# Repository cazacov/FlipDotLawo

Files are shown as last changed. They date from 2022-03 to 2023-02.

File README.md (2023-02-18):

# FlipDot34

Controller for the flip-dot display with 34-pin connector. For example produced by Lawo-Luminator-Europa Mark IV Industries GmbH.

Version 28x19
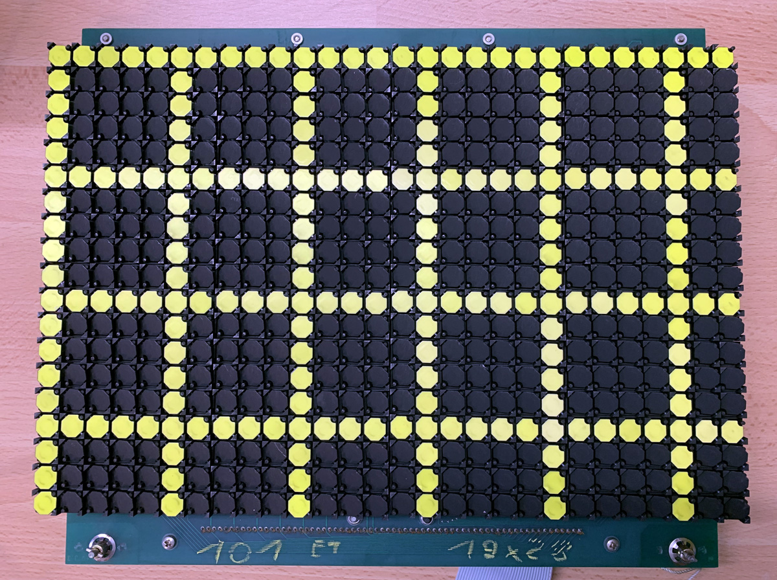
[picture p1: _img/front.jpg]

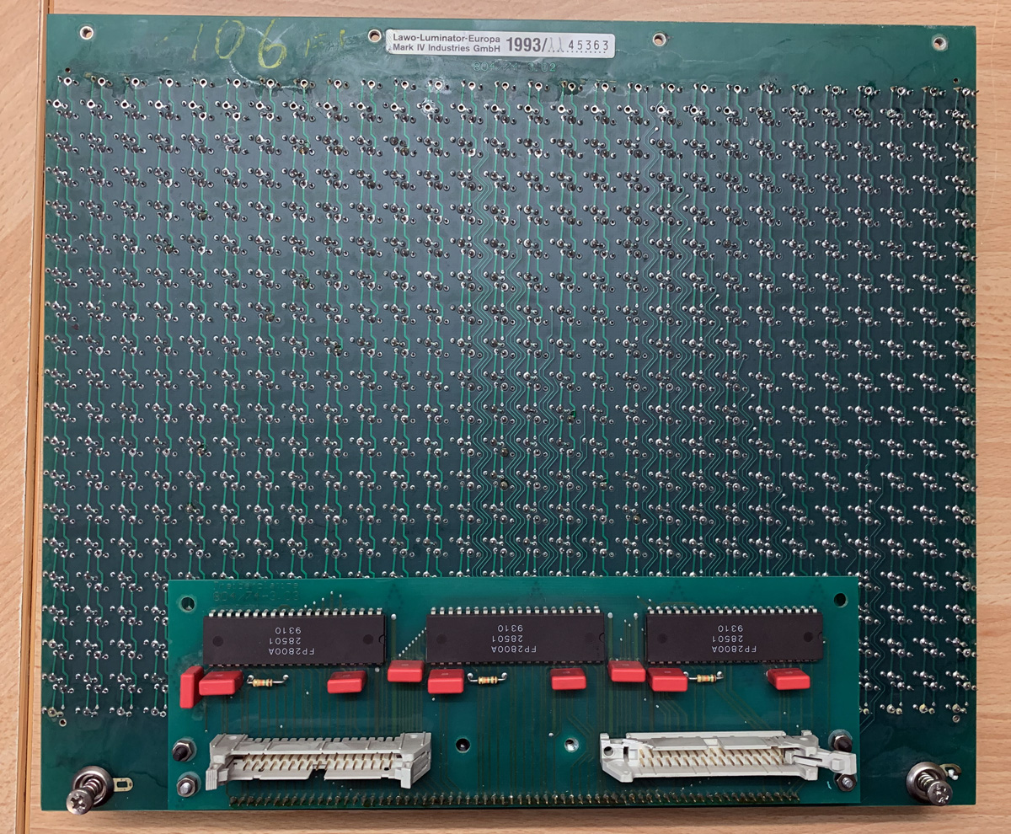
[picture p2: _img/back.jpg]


Version 28x24 with LED lights
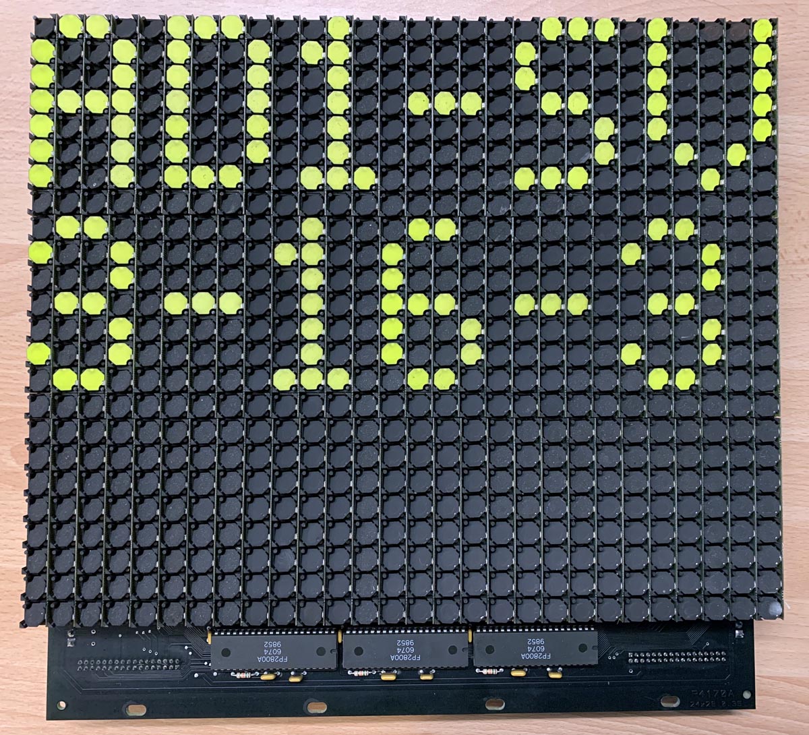
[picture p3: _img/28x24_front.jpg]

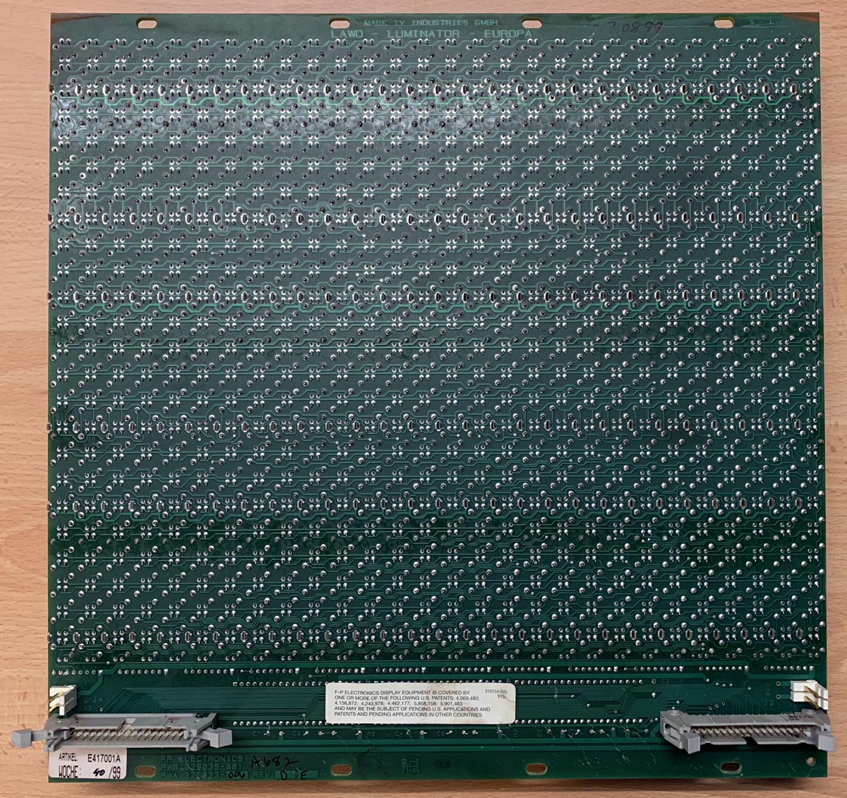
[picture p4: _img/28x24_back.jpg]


## Connector Pinout
| Pin |  Function | Pin |  Function |
| --- | --- | --- | --- |
| 1 | GND  | 2 | GND  | 
| 3 | GND  | 4 | GND  | 
| 5 | 5V  |  6 | 5V  | 
| 7 | A0-X | 8 | DATA-X |
| 9 | A1-X | 10 | ENABLE-Y-SET |
| 11 | A2-X | 12 | ENABLE-Y-RESET |e
| 13 | B0-X | 14 | ENABLE-X-1 |
| 15 | B1-X | 16 | ENABLE-X-2 |
| 17 | A0-Y | 18 | ENABLE-X-3 |
| 19 | A1-Y | 20 | ENABLE-X-4 |
| 21 | A2-Y | 22 | ENABLE-X-5 |
| 23 | B0-Y | 24 | ENABLE-X-6 |
| 25 | B1-Y | 26 | ENABLE-X-7 |
| 27 | n/c | 28 | ENABLE-X-8 |
| 29 | 24V  |  30 | 24V  | 
| 31 | GND  | 32 | GND  | 
| 33 | GND  | 34 | GND  | 

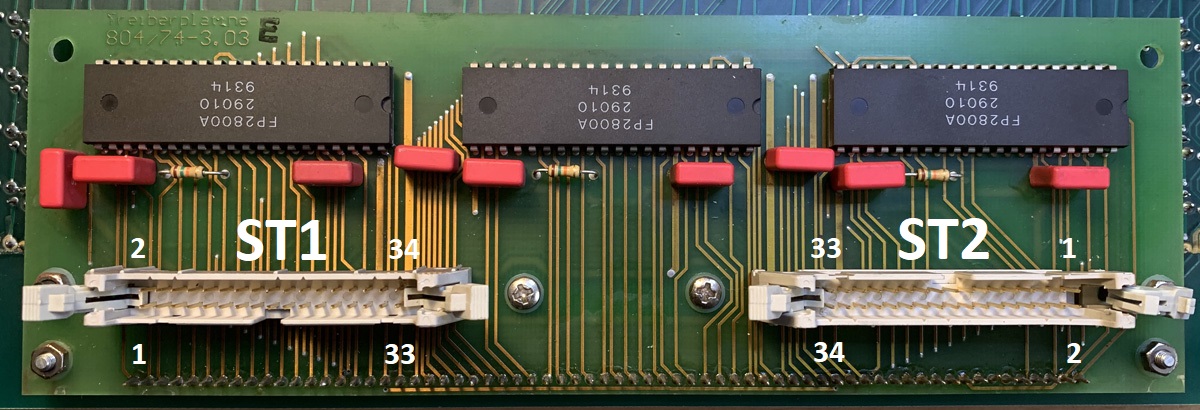
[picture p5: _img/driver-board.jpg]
Matrix driver


## Chaining Multiple Displays in a Row

Driver board has two connectors. The output connector ST2 mostly duplicates 1:1 singnals from the input ST1 but ENABLE-X- signals are shifted. 

| Pin | INPUT  ST1 |  OUTPUT ST2 |
| --- | --- | --- |
| 13  | ENABLE-X-1 | ENABLE-X-2 |
| 15  | ENABLE-X-2 | ENABLE-X-3 |
| 17  | ENABLE-X-3 | ENABLE-X-4 |
| 19  | ENABLE-X-4 | ENABLE-X-5 |
| 21  | ENABLE-X-5 | ENABLE-X-6 |
| 23  | ENABLE-X-6 | ENABLE-X-7 |
| 25  | ENABLE-X-7 | ENABLE-X-8 |
| 17  | ENABLE-X-8 | ENABLE-X-1 |

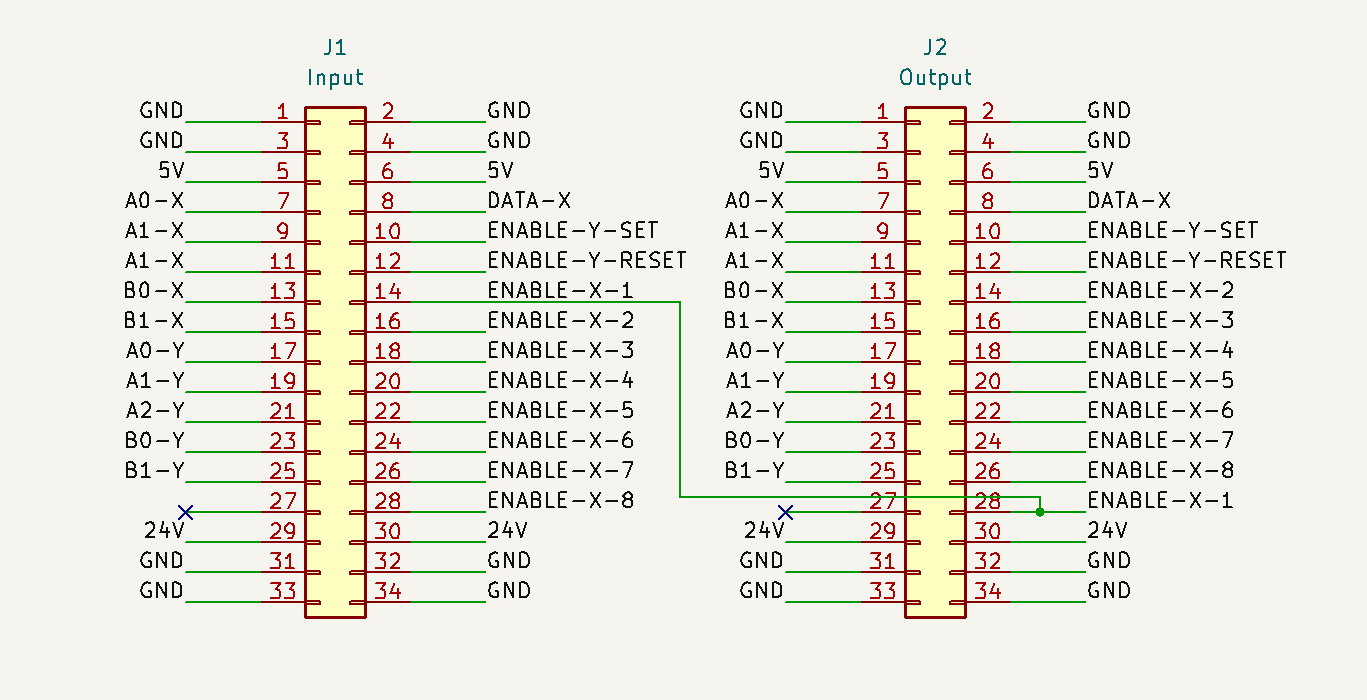
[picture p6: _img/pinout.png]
Pinout


The ENABLE input of FP2800 X Driver is always connected to ENABLE-X-1 connector pin. For example when ENABLE-X-3 is set to HIGH the first two displays in a row will ignore it, but after two decrements the signal will be applied to ENABLE-X-1 ST1 of the third display matrix and will activate it.

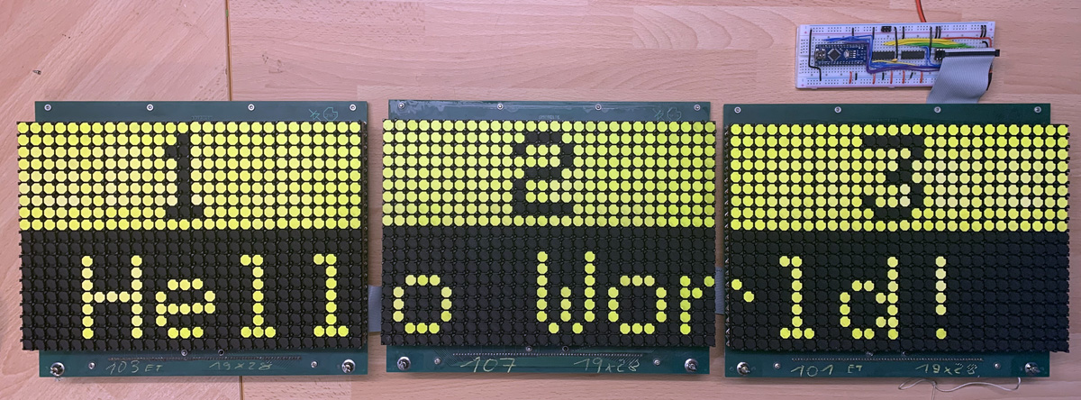
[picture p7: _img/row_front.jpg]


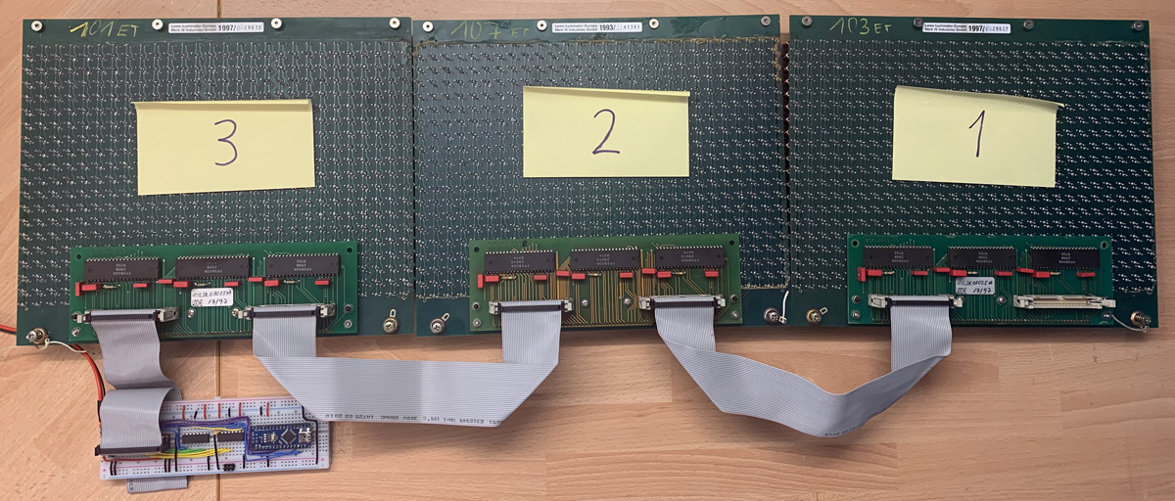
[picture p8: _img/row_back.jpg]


## Driver Boards

### Prototype

This prototype uses Arduino Nano and two 74HC595 shift registers to control up to 6 matrices. By adding another 595 it can control up to 8 display matrices.

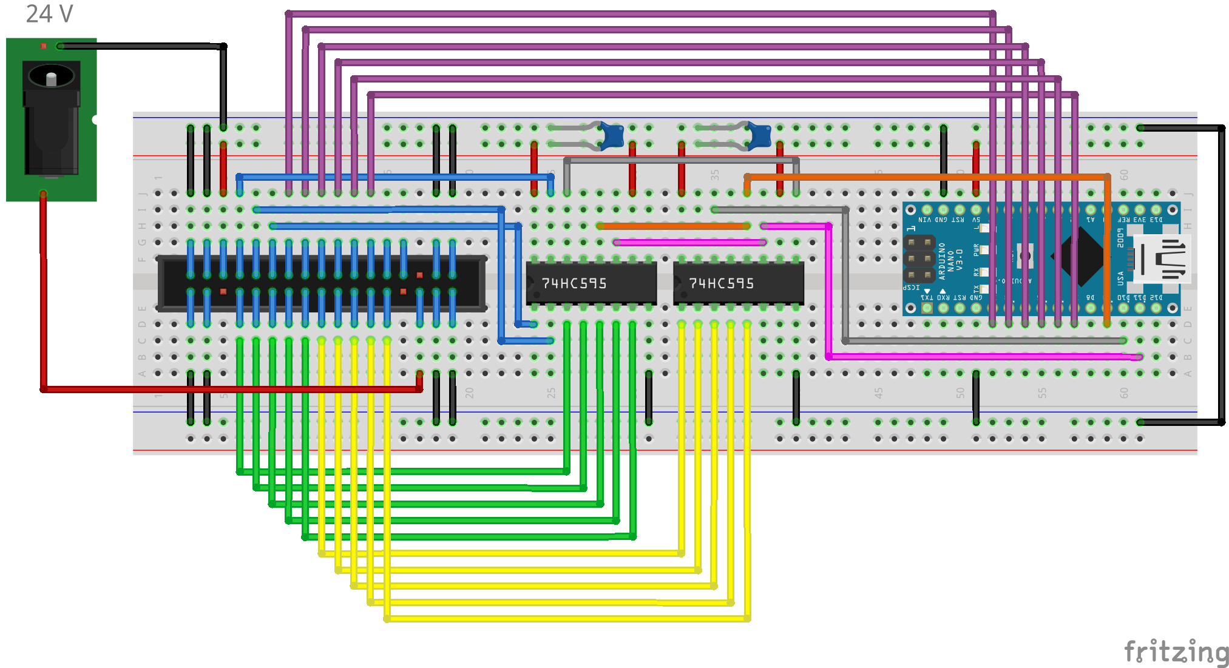
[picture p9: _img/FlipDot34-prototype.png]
Prototype


### FlipDot34Nano

Driver board with Arduino Nano and three 74HC595 shift registers opitmized for single-sided PCB that can be milled with 3018 CNC. 3 digital pins are used for controlling shift registers, analog pins A4 and A5 can be used to receive commands over I2C. Pins A0-A2 connected to DIP switches choosing I2C address.

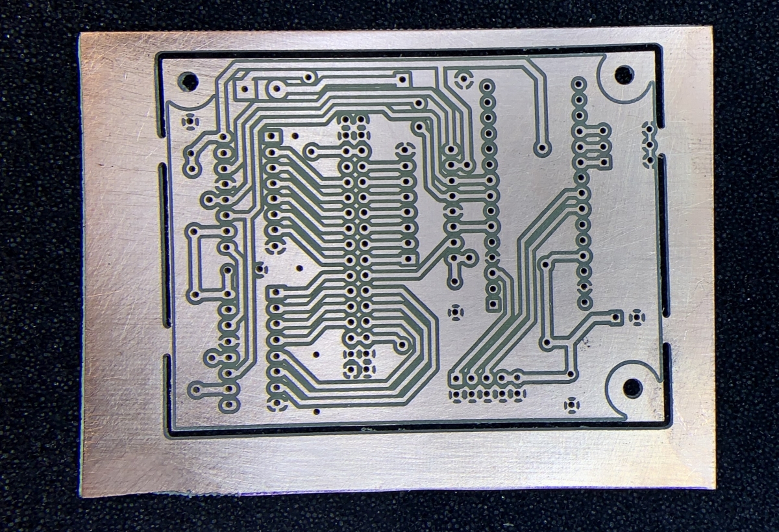
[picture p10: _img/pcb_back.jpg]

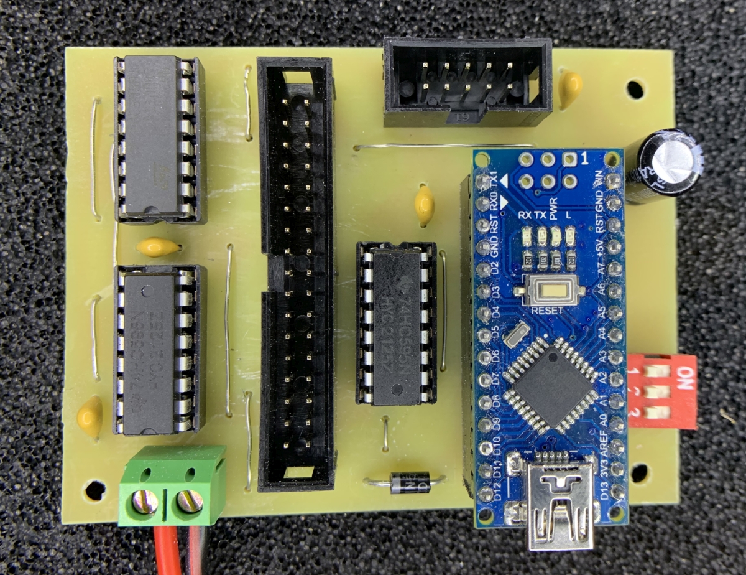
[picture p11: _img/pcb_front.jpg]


Schematic in KiCad 6 format checked in under .\Driver-boards\FlipDot34Nano\schematic\FlipDot34Nano

---
All trademarks, logos and brand names are the property of their respective owners. All company, product and service names are for identification purposes only. 

It's a hobby project; I am not affiliated with any  company producing flip-dot displays.

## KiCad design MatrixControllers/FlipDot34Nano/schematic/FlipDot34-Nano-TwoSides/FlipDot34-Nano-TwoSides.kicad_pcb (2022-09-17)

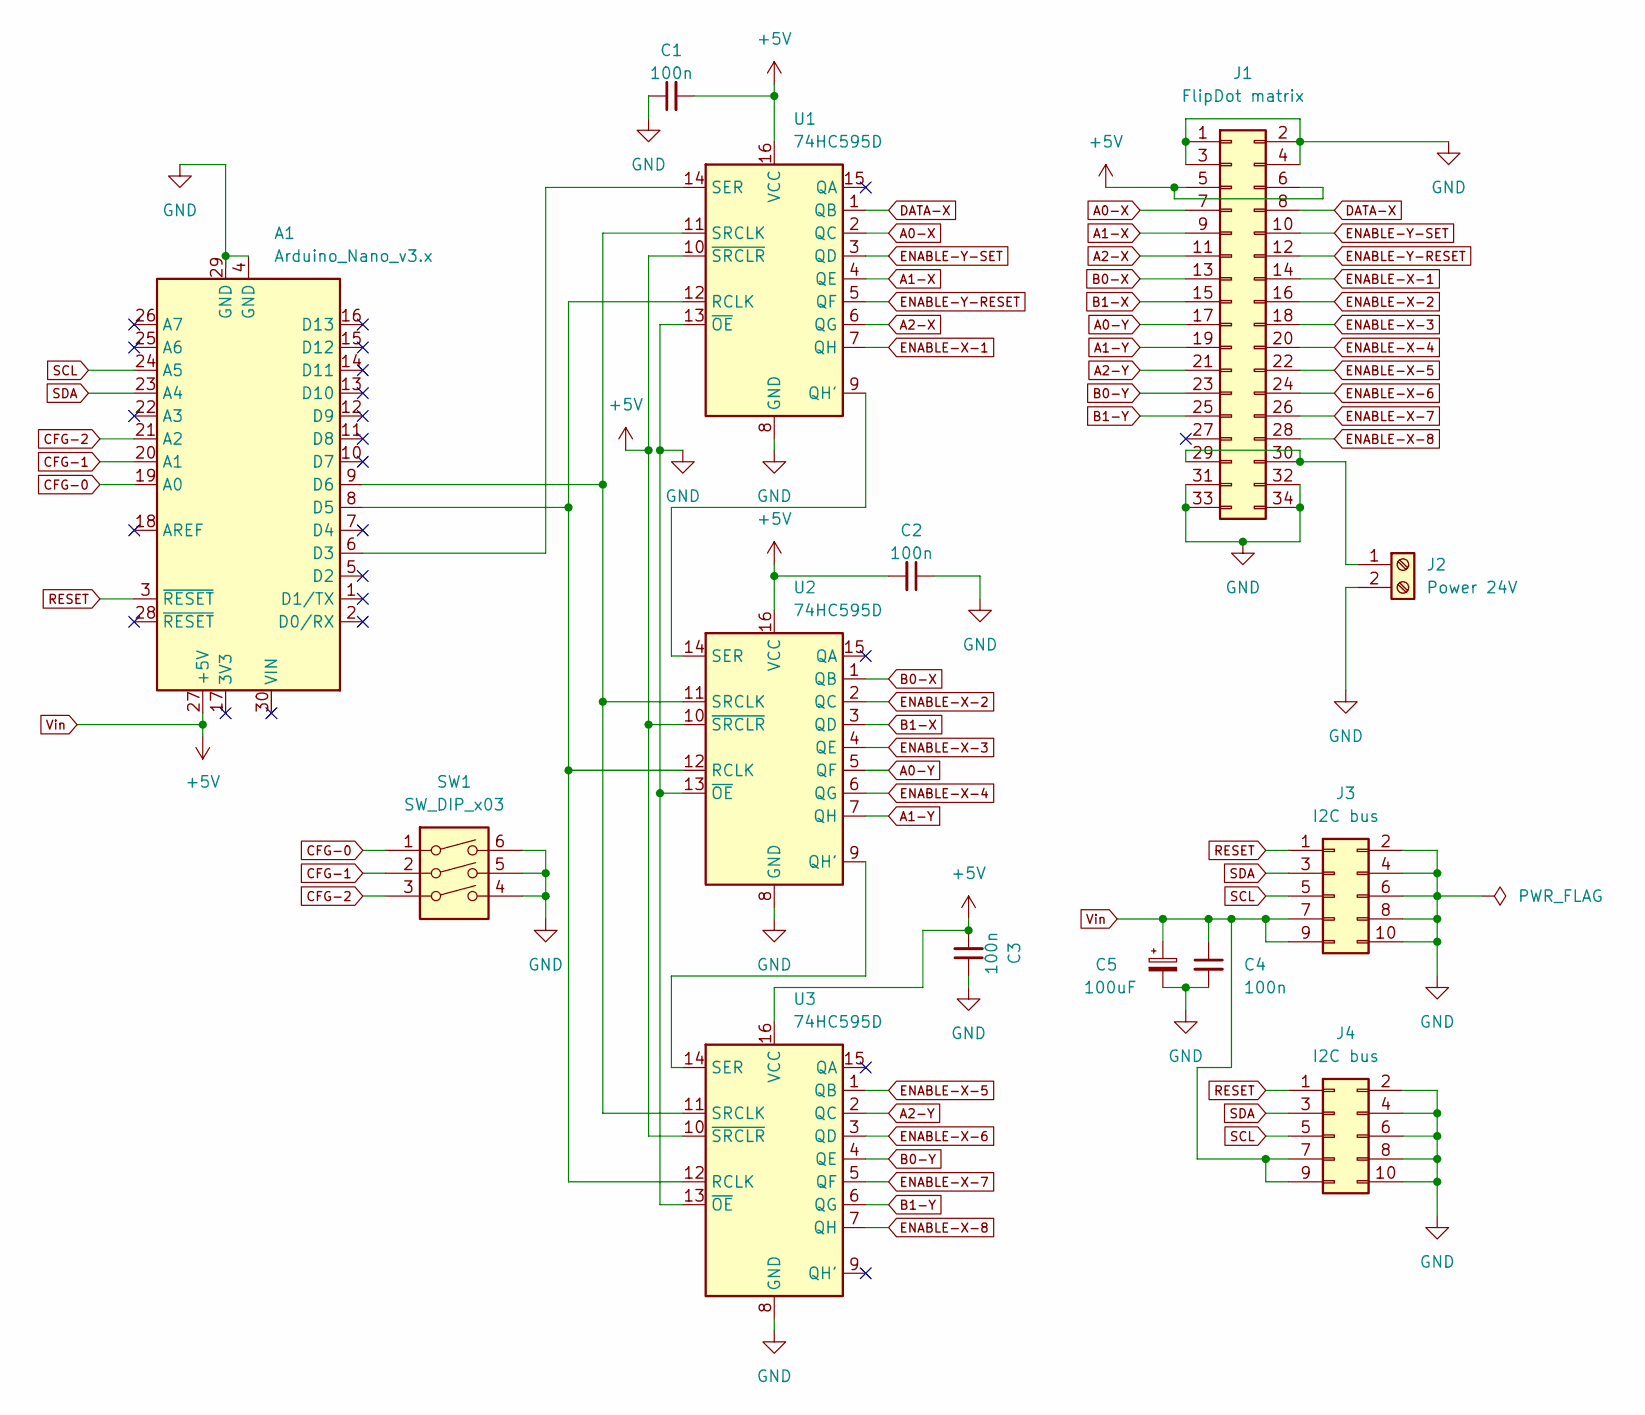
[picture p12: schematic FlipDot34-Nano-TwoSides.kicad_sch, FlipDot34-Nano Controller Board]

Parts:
A1: Arduino_Nano_v3.x; Arduino_Nano
C1, C2, C3, C4: 100n; C_1206_3216Metric_Pad1.33x1.80mm_HandSolder
C5: 100uF; CP_Radial_D8.0mm_P3.50mm
J1: FlipDot matrix; PinSocket_2x17_P2.54mm_Vertical
J2: Power 24V; TerminalBlock_bornier-2_P5.08mm
J3, J4: I2C bus; IDC-Header_2x05_P2.54mm_Vertical
SW1: SW_DIP_x03; SW_DIP_SPSTx03_Slide_9.78x9.8mm_W7.62mm_P2.54mm
U1, U2, U3: 74HC595D; SO-16_3.9x9.9mm_P1.27mm

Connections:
A0-X: J1.7, U1.2 (QC)
A0-Y: J1.17, U2.5 (QF)
A1-X: J1.9, U1.4 (QE)
A1-Y: J1.19, U2.7 (QH)
A2-X: J1.11, U1.6 (QG)
A2-Y: J1.21, U3.2 (QC)
B0-X: J1.13, U2.1 (QB)
B0-Y: J1.23, U3.4 (QE)
B1-X: J1.15, U2.3 (QD)
B1-Y: J1.25, U3.6 (QG)
CFG-0: A1.19 (A0), SW1.1
CFG-1: A1.20 (A1), SW1.2
CFG-2: A1.21 (A2), SW1.3
DATA-X: J1.8, U1.1 (QB)
ENABLE-X-1: J1.14, U1.7 (QH)
ENABLE-X-2: J1.16, U2.2 (QC)
ENABLE-X-3: J1.18, U2.4 (QE)
ENABLE-X-4: J1.20, U2.6 (QG)
ENABLE-X-5: J1.22, U3.1 (QB)
ENABLE-X-6: J1.24, U3.3 (QD)
ENABLE-X-7: J1.26, U3.5 (QF)
ENABLE-X-8: J1.28, U3.7 (QH)
ENABLE-Y-RESET: J1.12, U1.5 (QF)
ENABLE-Y-SET: J1.10, U1.3 (QD)
GND: A1.4 (GND), A1.29 (GND), C1.1, C2.1, C3.1, C4.2, C5.2, J1.1, J1.2, J1.3, J1.4, J1.31, J1.32, J1.33, J1.34, J2.2, J3.2, J3.4, J3.6, J3.8, J3.10, J4.2, J4.4, J4.6, J4.8, J4.10, SW1.4, SW1.5, SW1.6, U1.8 (GND), U1.13 (~OE), U2.8 (GND), U2.13 (~OE), U3.8 (GND), U3.13 (~OE)
unnamed: A1.6 (D3), U1.14 (SER)
unnamed: A1.8 (D5), U1.12 (RCLK), U2.12 (RCLK), U3.12 (RCLK)
unnamed: A1.9 (D6), U1.11 (SRCLK), U2.11 (SRCLK), U3.11 (SRCLK)
unnamed: J1.29, J1.30, J2.1
unnamed: U1.9 (QH'), U2.14 (SER)
unnamed: U2.9 (QH'), U3.14 (SER)
RESET: A1.3 (~RESET), J3.1, J4.1
SCL: A1.24 (A5), J3.5, J4.5
SDA: A1.23 (A4), J3.3, J4.3
Vin: A1.27 (+5V), C1.2, C2.2, C3.2, C4.1, C5.1, J1.5, J1.6, J3.7, J3.9, J4.7, J4.9, U1.10 (~SRCLR), U1.16 (VCC), U2.10 (~SRCLR), U2.16 (VCC), U3.10 (~SRCLR), U3.16 (VCC)

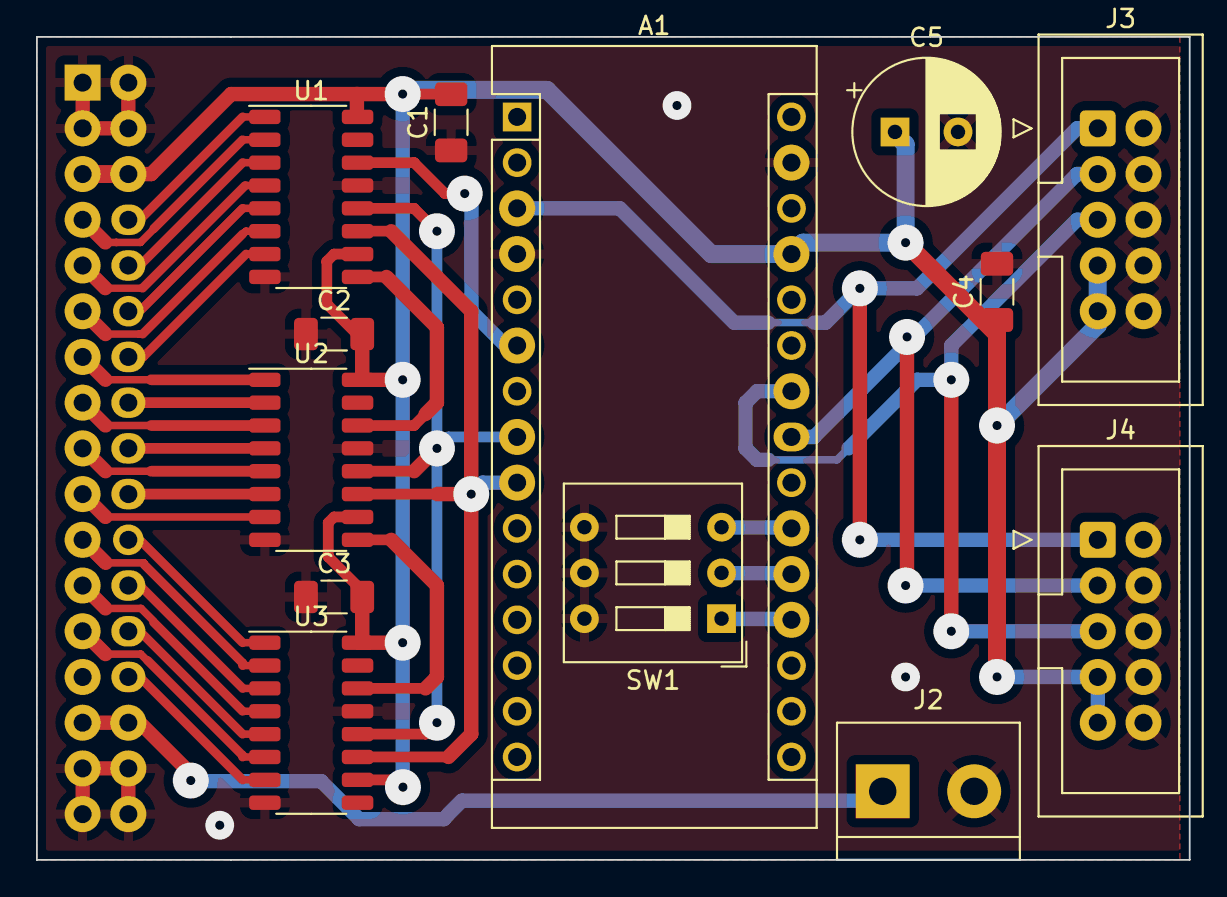
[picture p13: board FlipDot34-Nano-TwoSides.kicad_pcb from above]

Board: 2 copper layers, 64.0 x 45.7 mm, 14 parts (1 on the bottom side), 35 nets.

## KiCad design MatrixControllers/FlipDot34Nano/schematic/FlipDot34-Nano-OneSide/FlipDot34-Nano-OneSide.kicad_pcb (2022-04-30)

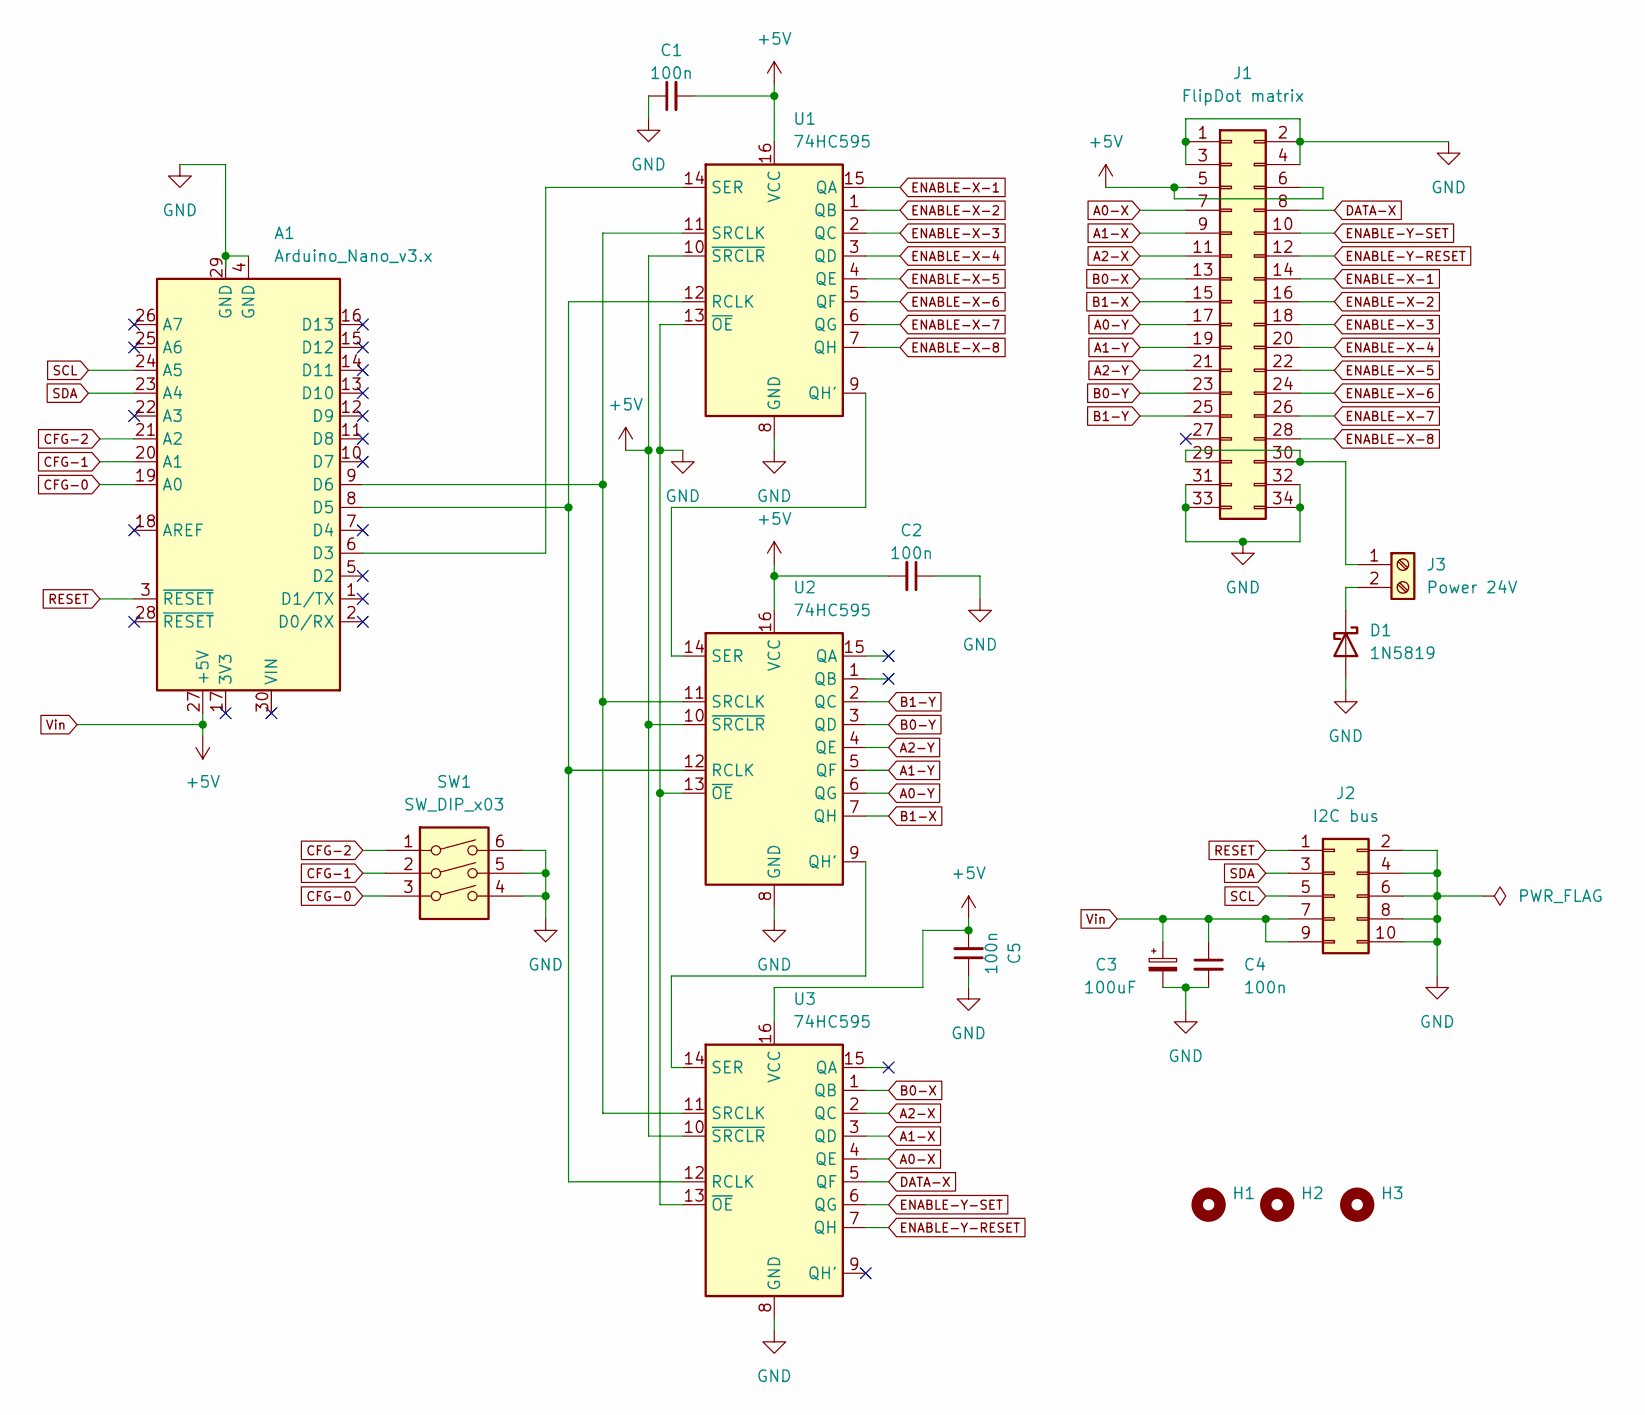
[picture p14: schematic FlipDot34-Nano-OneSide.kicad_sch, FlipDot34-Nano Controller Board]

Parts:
A1: Arduino_Nano_v3.x; Arduino_Nano
C1, C2, C4, C5: 100n; C_Disc_D5.0mm_W2.5mm_P5.00mm
C3: 100uF; CP_Radial_D8.0mm_P3.50mm
D1: 1N5819; D_DO-41_SOD81_P10.16mm_Horizontal
H1, H2, H3: MountingHole; MountingHole_3.2mm_M3
J1: FlipDot matrix; IDC-Header_2x17_P2.54mm_Vertical
J2: I2C bus; IDC-Header_2x05_P2.54mm_Vertical
J3: Power 24V; TerminalBlock_bornier-2_P5.08mm
SW1: SW_DIP_x03; SW_DIP_SPSTx03_Slide_9.78x9.8mm_W7.62mm_P2.54mm
U1, U2, U3: 74HC595; DIP-16_W7.62mm_LongPads

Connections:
A0-X: J1.7, U3.4 (QE)
A0-Y: J1.17, U2.6 (QG)
A1-X: J1.9, U3.3 (QD)
A1-Y: J1.19, U2.5 (QF)
A2-X: J1.11, U3.2 (QC)
A2-Y: J1.21, U2.4 (QE)
B0-X: J1.13, U3.1 (QB)
B0-Y: J1.23, U2.3 (QD)
B1-X: J1.15, U2.7 (QH)
B1-Y: J1.25, U2.2 (QC)
CFG-0: A1.19 (A0), SW1.3
CFG-1: A1.20 (A1), SW1.2
CFG-2: A1.21 (A2), SW1.1
DATA-X: J1.8, U3.5 (QF)
ENABLE-X-1: J1.14, U1.15 (QA)
ENABLE-X-2: J1.16, U1.1 (QB)
ENABLE-X-3: J1.18, U1.2 (QC)
ENABLE-X-4: J1.20, U1.3 (QD)
ENABLE-X-5: J1.22, U1.4 (QE)
ENABLE-X-6: J1.24, U1.5 (QF)
ENABLE-X-7: J1.26, U1.6 (QG)
ENABLE-X-8: J1.28, U1.7 (QH)
ENABLE-Y-RESET: J1.12, U3.7 (QH)
ENABLE-Y-SET: J1.10, U3.6 (QG)
GND: A1.4 (GND), A1.29 (GND), C1.1, C2.1, C3.2, C4.2, C5.1, D1.2 (A), J1.1, J1.2, J1.3, J1.4, J1.31, J1.32, J1.33, J1.34, J2.2, J2.4, J2.6, J2.8, J2.10, SW1.4, SW1.5, SW1.6, U1.8 (GND), U1.13 (~OE), U2.8 (GND), U2.13 (~OE), U3.8 (GND), U3.13 (~OE)
unnamed: A1.6 (D3), U1.14 (SER)
unnamed: A1.8 (D5), U1.12 (RCLK), U2.12 (RCLK), U3.12 (RCLK)
unnamed: A1.9 (D6), U1.11 (SRCLK), U2.11 (SRCLK), U3.11 (SRCLK)
unnamed: D1.1 (K), J3.2
unnamed: J1.29, J1.30, J3.1
unnamed: U1.9 (QH'), U2.14 (SER)
unnamed: U2.9 (QH'), U3.14 (SER)
RESET: A1.3 (~RESET), J2.1
SCL: A1.24 (A5), J2.5
SDA: A1.23 (A4), J2.3
Vin: A1.27 (+5V), C1.2, C2.2, C3.1, C4.1, C5.2, J1.5, J1.6, J2.7, J2.9, U1.10 (~SRCLR), U1.16 (VCC), U2.10 (~SRCLR), U2.16 (VCC), U3.10 (~SRCLR), U3.16 (VCC)

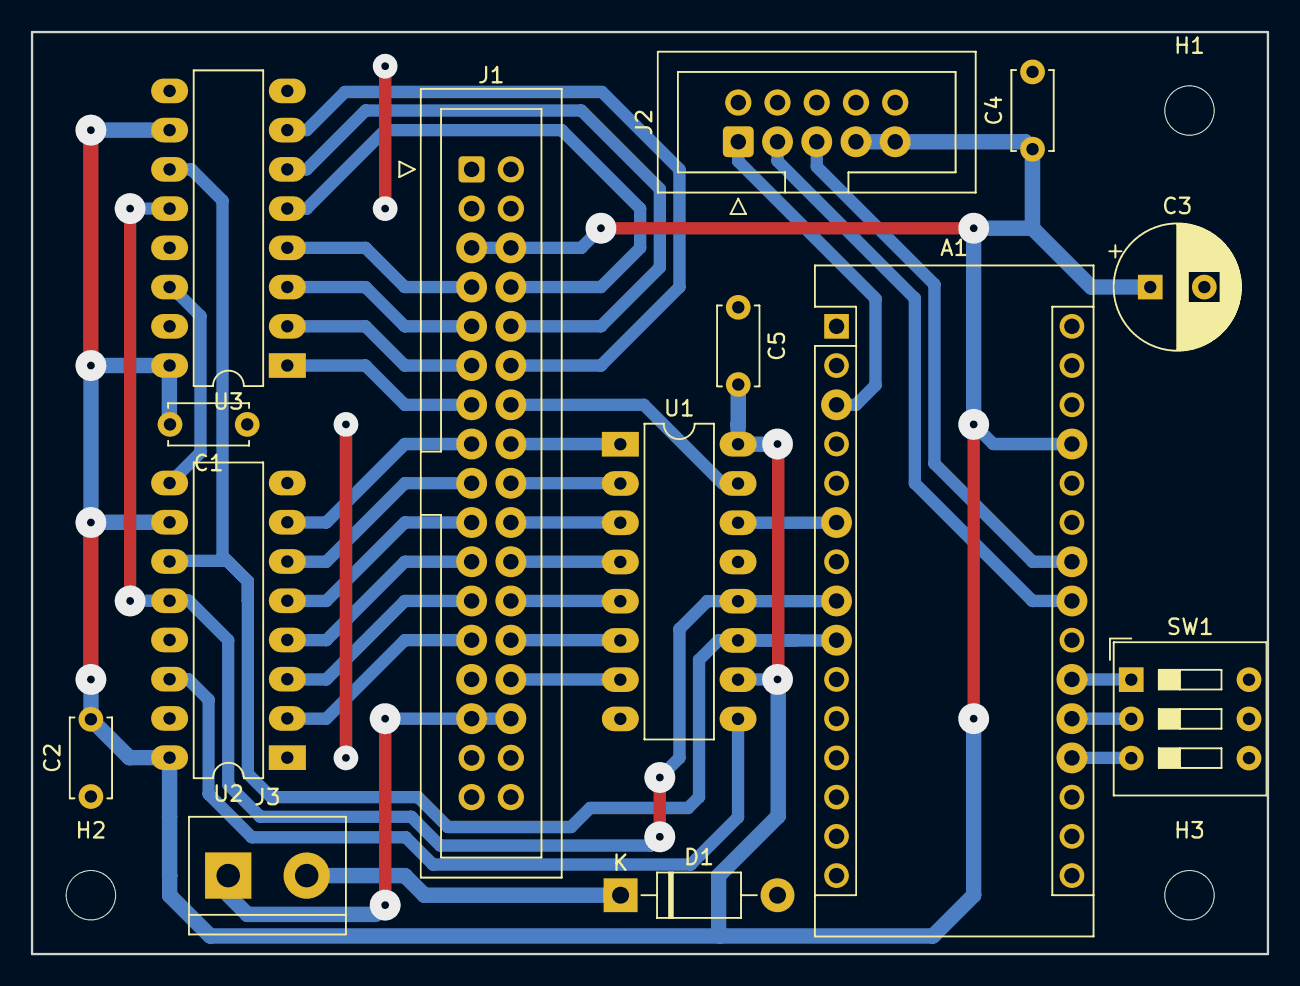
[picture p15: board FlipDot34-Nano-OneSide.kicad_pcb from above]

Board: 2 copper layers, 80.0 x 59.7 mm, 17 parts (0 on the bottom side), 36 nets.

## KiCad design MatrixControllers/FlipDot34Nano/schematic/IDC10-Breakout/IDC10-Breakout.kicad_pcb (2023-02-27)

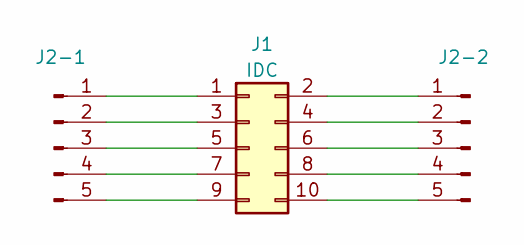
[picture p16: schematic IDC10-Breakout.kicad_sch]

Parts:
J1: IDC; IDC-Header_2x05_P2.54mm_Vertical
J2-1, J2-2: PinHeader_1x05_P2.54mm_Vertical

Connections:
unnamed: J1.1, J2-1.1
unnamed: J1.2, J2-2.1
unnamed: J1.3, J2-1.2
unnamed: J1.4, J2-2.2
unnamed: J1.5, J2-1.3
unnamed: J1.6, J2-2.3
unnamed: J1.7, J2-1.4
unnamed: J1.8, J2-2.4
unnamed: J1.9, J2-1.5
unnamed: J1.10, J2-2.5

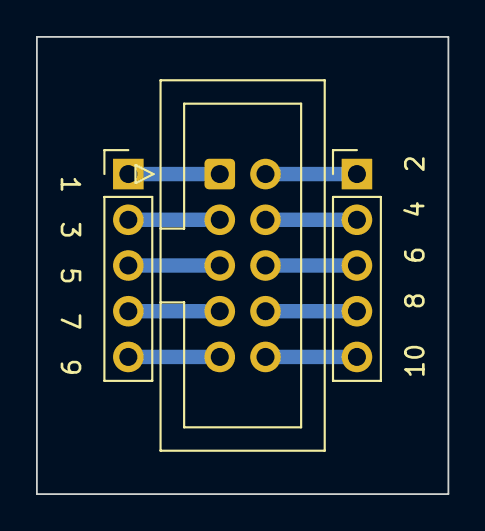
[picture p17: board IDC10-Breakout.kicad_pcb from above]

Board: 2 copper layers, 22.9 x 25.4 mm, 3 parts (0 on the bottom side), 10 nets.

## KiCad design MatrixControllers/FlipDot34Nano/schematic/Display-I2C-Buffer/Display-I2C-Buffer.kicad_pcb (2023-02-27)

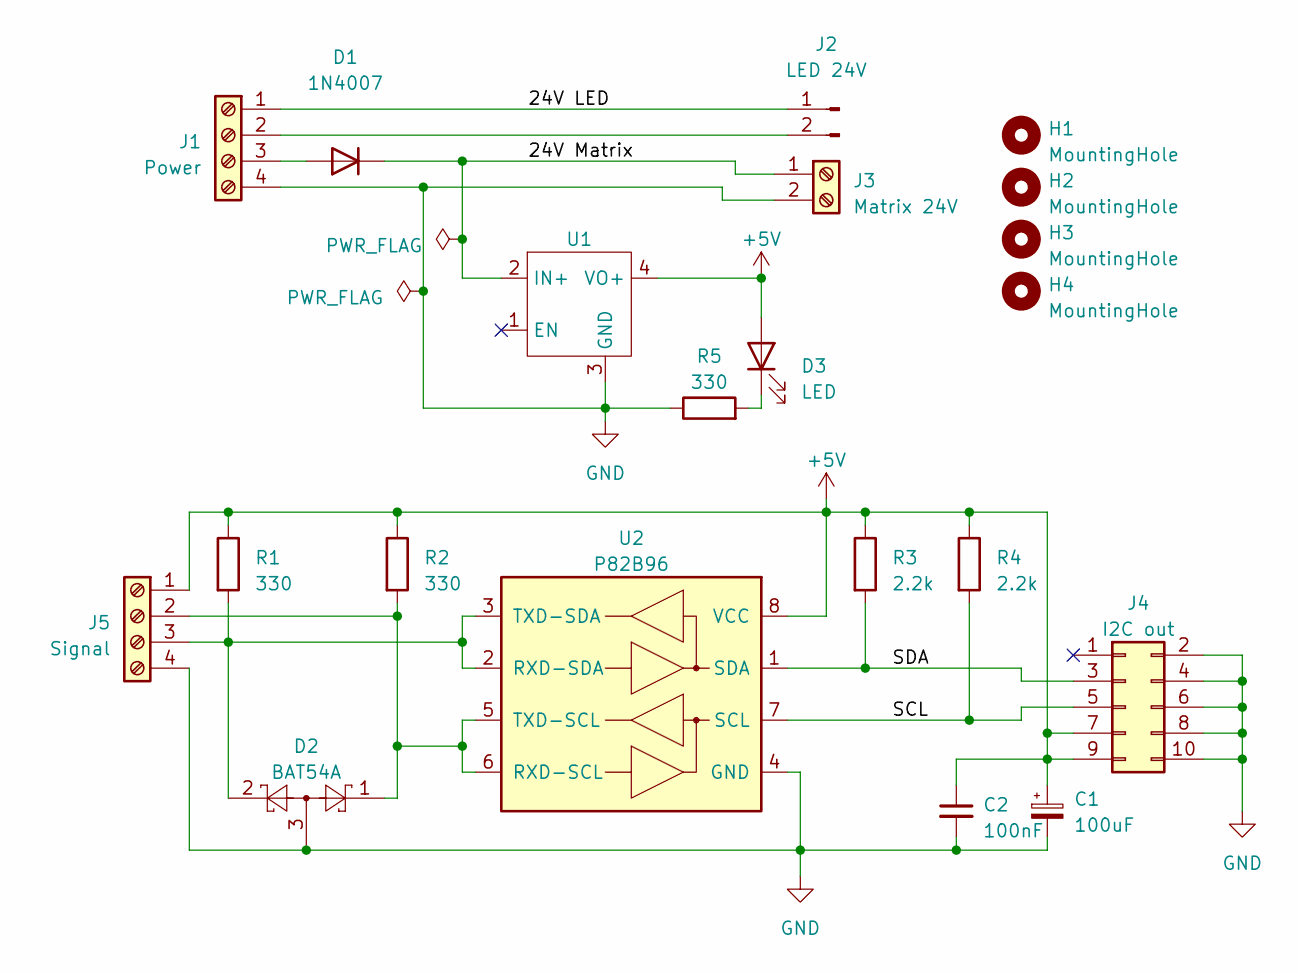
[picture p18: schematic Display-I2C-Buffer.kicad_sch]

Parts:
C1: 100uF; CP_Radial_D8.0mm_P3.50mm
C2: 100nF; C_1206_3216Metric
D1: 1N4007; D_DO-41_SOD81_P10.16mm_Horizontal
D2: BAT54A; SOT-23
D3: LED; LED_0805_2012Metric
H1, H2, H3, H4: MountingHole; MountingHole_3.2mm_M3_DIN965
J1: Power; TerminalBlock_bornier-4_P5.08mm
J2: LED 24V; Molex_KK-396_A-41791-0002_1x02_P3.96mm_Vertical
J3: Matrix 24V; TerminalBlock_bornier-2_P5.08mm
J4: I2C out; IDC-Header_2x05_P2.54mm_Vertical
J5: Signal; JST_EH_B4B-EH-A_1x04_P2.50mm_Vertical
R1, R2, R5: 330; R_1206_3216Metric
R3, R4: 2.2k; R_1206_3216Metric
U1: Mini DC-DC
U2: P82B96; SOIC-8_3.9x4.9mm_P1.27mm

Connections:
+5V: C1.1, C2.1, D3.2 (A), J4.7, J4.9, J5.1, R1.1, R2.1, R3.1, R4.1, U1.4 (VO+), U2.8 (VCC)
/24V LED: J1.1, J2.1
/24V Matrix: D1.1 (K), J3.1, U1.2 (IN+)
/SCL: J4.5, R4.2, U2.7 (SCL)
/SDA: J4.3, R3.2, U2.1 (SDA)
GND: C1.2, C2.2, D2.3, J1.4, J3.2, J4.2, J4.4, J4.6, J4.8, J4.10, J5.4, R5.1, U1.3 (GND), U2.4 (GND)
unnamed: D1.2 (A), J1.3
unnamed: D3.1 (K), R5.2
unnamed: J1.2, J2.2
unnamed: D2.1, J5.2, R2.2, U2.5 (TXD-SCL), U2.6 (RXD-SCL)
unnamed: D2.2, J5.3, R1.2, U2.2 (RXD-SDA), U2.3 (TXD-SDA)

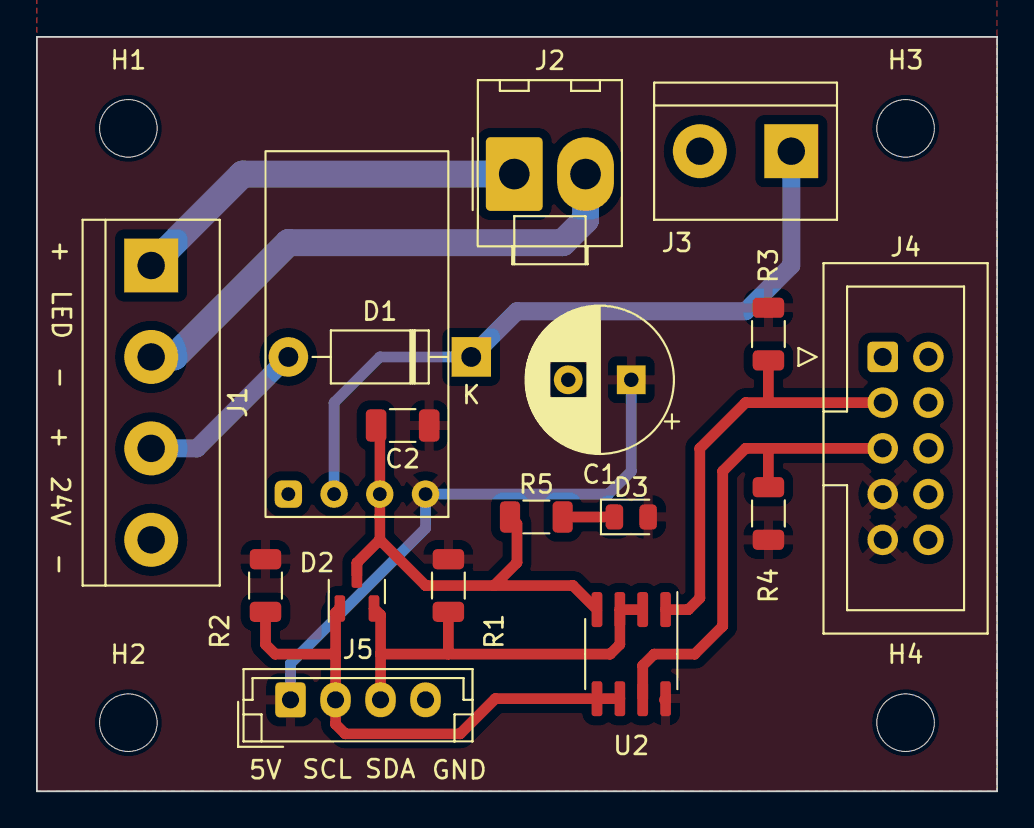
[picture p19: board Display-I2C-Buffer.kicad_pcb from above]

Board: 2 copper layers, 53.3 x 41.9 mm, 21 parts (0 on the bottom side), 11 nets.

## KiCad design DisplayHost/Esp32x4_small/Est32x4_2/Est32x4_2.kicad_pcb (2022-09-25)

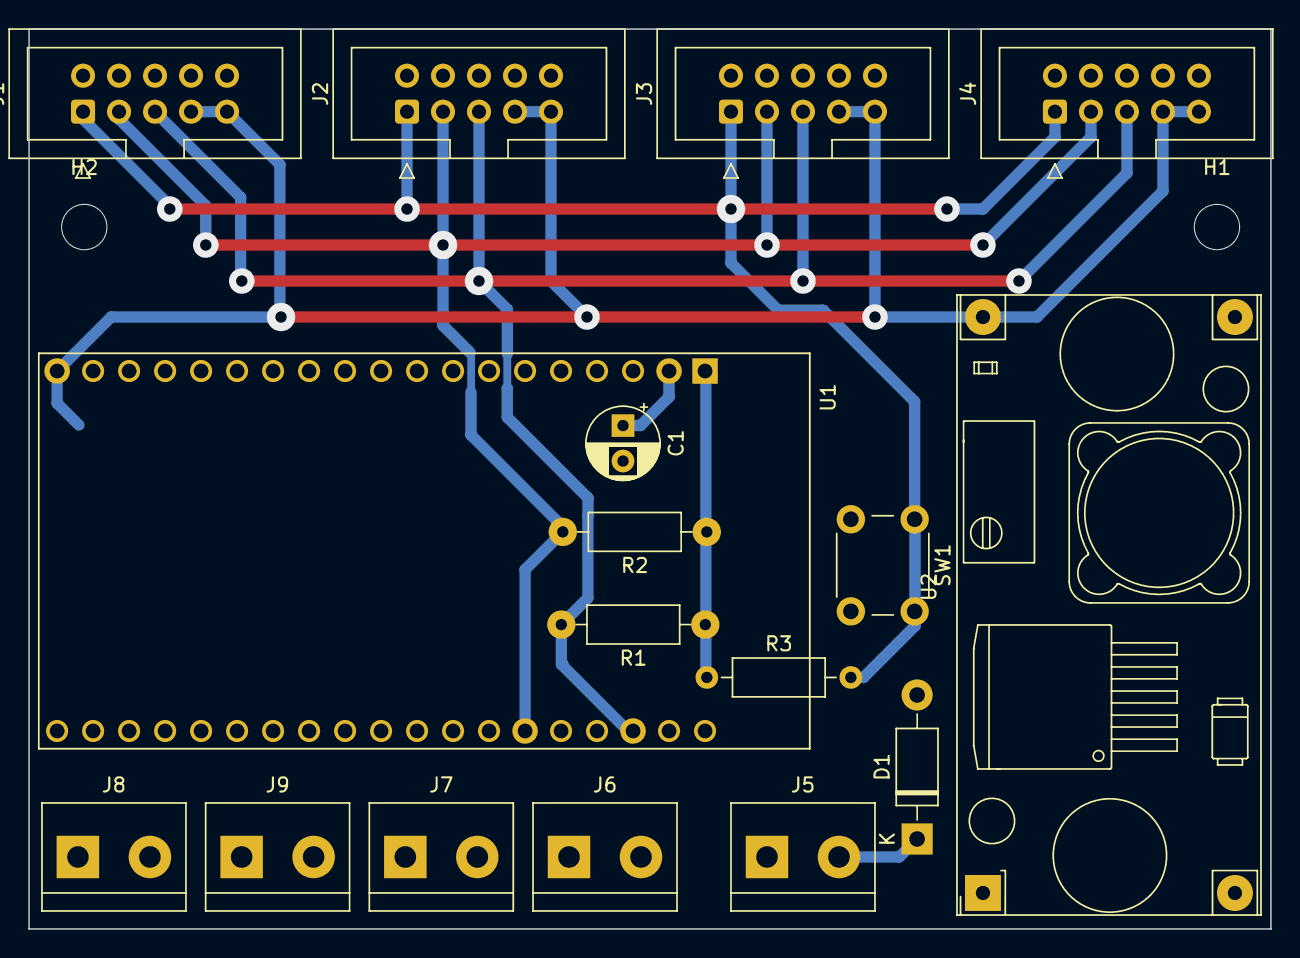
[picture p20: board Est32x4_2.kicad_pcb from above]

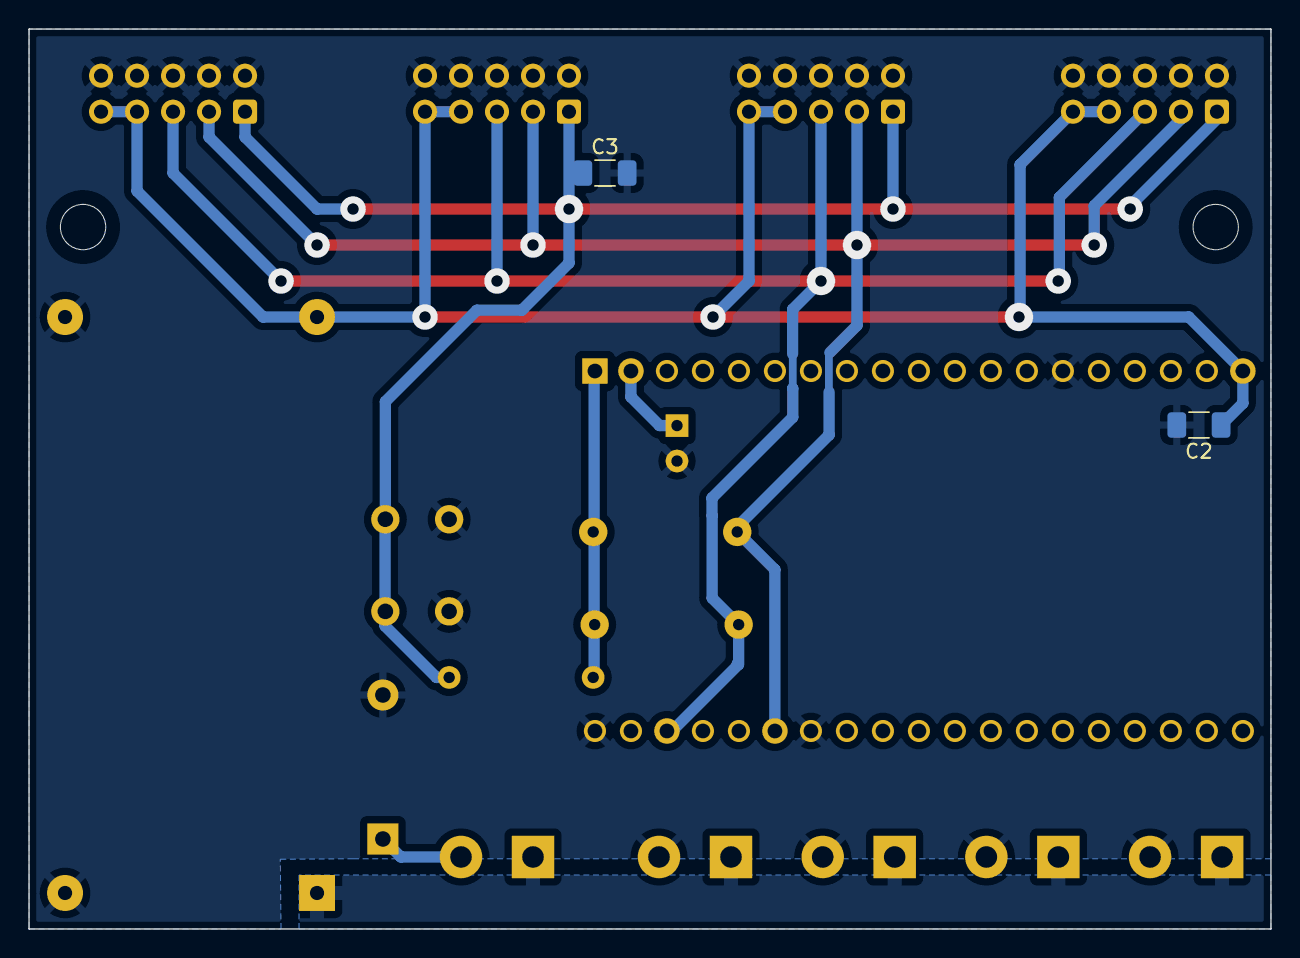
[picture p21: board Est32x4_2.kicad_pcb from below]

Board: 2 copper layers, 87.6 x 63.5 mm, 21 parts (2 on the bottom side), 9 nets.

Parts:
C1: 10uF; CP_Radial_D5.0mm_P2.50mm
C2, C3: 100n; C_1206_3216Metric_Pad1.33x1.80mm_HandSolder
D1: 1N5819; D_DO-41_SOD81_P10.16mm_Horizontal
H1, H2: MountingHole; MountingHole_3.2mm_M3
J1, J2, J3, J4: I2C bus; IDC-Header_2x05_P2.54mm_Vertical
J5: 24V In; TerminalBlock_bornier-2_P5.08mm
J6, J7, J8, J9: 24V Out; TerminalBlock_bornier-2_P5.08mm
R1, R2, R3: 10k; R_Axial_DIN0207_L6.3mm_D2.5mm_P10.16mm_Horizontal
SW1: SW_Push_Dual; SW_PUSH_6mm_H5mm
U1: ESP32-DEVKITC-32D; MODULE_ESP32-DEVKITC-32D
U2: DC-DC StepDown 5V; DCDC_StepDown_LM2596

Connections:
GND: C1.2, C2.2, C3.2, D1.2 (A), J1.2, J1.4, J1.6, J1.8, J1.10, J2.2, J2.4, J2.6, J2.8, J2.10, J3.2, J3.4, J3.6, J3.8, J3.10, J4.2, J4.4, J4.6, J4.8, J4.10, J6.2, J7.2, J8.2, J9.2, SW1.2, U1.14 (GND1), U1.20 (GND3), U1.26 (GND2), U2.2 (GND), U2.3 (GND)
unnamed: C1.1, U1.2 (EN)
unnamed: D1.1 (K), J5.2
RESET: C3.1, J1.1, J2.1, J3.1, J4.1, R3.2, SW1.1
SCL: J1.5, J2.5, J3.5, J4.5, R1.2, U1.22 (IO22)
SDA: J1.3, J2.3, J3.3, J4.3, R2.2, U1.25 (IO21)
VCC: R1.1, R2.1, R3.1, U1.1 (3V3)
VOut: C2.1, J1.7, J1.9, J2.7, J2.9, J3.7, J3.9, J4.7, J4.9, U1.19 (EXT_5V), U2.4 (Vout)
Vin: J5.1, J6.1, J7.1, J8.1, J9.1, U2.1 (Vin)

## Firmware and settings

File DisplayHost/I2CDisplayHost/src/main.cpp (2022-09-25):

#include <Arduino.h>
#include <Wire.h>
#include "frames56x38.h"
#include "CommandSender.h"

const int senders_count = 4;
const int play_every = 1;
const int frame_count = 1158;

const uint8_t addresses[senders_count] = {
  0x20,
  0x21,
  0x22,
  0x23
};

CommandSender senders[senders_count];

//const int frame_count = sizeof(frames38x28) / sizeof(frames38x28[0]);

void setup()
{
  // put your setup code here, to run once:

  //Wire.begin(sdaPin, sclPin );
  //Wire.setClock(400000);
  Serial.begin(115200);
  delay(5000);

  for (int i = 0; i < senders_count; i++) {
    senders[i].begin(addresses[i]);
  }

  for (int i = 0; i < senders_count; i++) {
    senders[i].setDelays(100);
    senders[i].fill_screen();
    delay(500);
    senders[i].clear_screen();
    delay(500);
  }
  delay(1000);
}

uint16_t frame_nr = 0;

void loop()
{

  uint8_t buf[80];

  long ms = millis();
  for (int sender = 0; sender < senders_count; sender++) {
    for (int i = 0; i < 76; i++)
    {
      buf[i] = pgm_read_byte(&(frames56x38[frame_nr][sender][i]));
    }
    senders[sender].bitmap(buf);
  }
  frame_nr += play_every;
  if (frame_nr >= frame_count)
  {
    frame_nr = 0;
  }
//  Serial.println(frame_nr);
  int frame_length = 1000 * play_every / 5;

  long left = frame_length + ms - millis();
  Serial.println(left);
  if (left > 0)
  {
    delay(left);
  }
  else
  {
    delay(2);
  }

  return;
}

/*
void sendFrame(int frame_nr) {
  Wire.beginTransmission(I2C_ADDRESS); 
  Wire.write(0x89);              
  Wire.write(0);              
  Wire.write(0);
  Wire.write(28);
  Wire.write(19);

  for (int i = 0; i < 19; i++) {
    for (int j = 0; j < 4; j++) {

      int offset = i * 4 + j;

      Wire.write(pgm_read_byte(&(frames[frame_nr][offset])));
    }
    if (i % 5 == 4) {
      Wire.endTransmission();
      delay(80); 
      Wire.beginTransmission(I2C_ADDRESS); 
    }
  }
  Wire.endTransmission(); 
  Serial.println(frame_nr);  
}
*/

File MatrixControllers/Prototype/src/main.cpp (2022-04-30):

#include <Arduino.h>
#include "flipDot34GFX.h"


FlipDot34GFX display(28, 19, 1, StackMode::kStacked);

void setup() {
  // 2 columns of matrices, each 28x19 dots
  Serial.begin(115200);
  display.setRotation(3);

  display.startWrite();
  display.fillScreen(0); 
  display.endWrite();
}

int color = 1;

void loop() {
  for (int y = 0; y < display.height(); y++) {
    for (int x = 0; x < display.width(); x++) {
      display.startWrite();
      display.drawPixel(x, y, color);
      display.endWrite();
      delay(5);
    }
  }
  delay(3000);
  color = 1 - color;
}

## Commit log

2022-03-27 Driver for Lawo flip-dot displays
    [driver-board.kicad_pcb, driver-board.kicad_sch]
2022-04-06 Improve performance with frame buffer
2022-04-09 Document chaining of displays
2022-04-11 Add controller schematic
    [FlipDot34.fzz, flipdot34.kicad_pcb, flipdot34.kicad_sch]
2022-04-12 Schematic - add communication and config connectors
    [flipdot34.kicad_sch]
2022-04-13 Add +24V terminal
    [flipdot34.kicad_sch]
2022-04-13 Assign footprints
    [flipdot34.kicad_sch]
2022-04-14 Add board dimensions
    [flipdot34.kicad_pcb, flipdot34.kicad_sch]
2022-04-14 Add mounting holes
    [flipdot34.kicad_pcb, flipdot34.kicad_sch]
2022-04-15 DRC tests pass
    [flipdot34.kicad_pcb, flipdot34.kicad_sch]
2022-04-15 Minor fixes
    [flipdot34.kicad_pcb]
2022-05-01 Add FlipDot34Esp board
    [FlipDot34Esp.kicad_pcb, FlipDot34Esp.kicad_sch]
2022-05-04 Design 2-sided PCB
    [FlipDot34NanoSMD.kicad_pcb, FlipDot34NanoSMD.kicad_sch]
2022-05-05 Add ground polygon
    [FlipDot34NanoSMD.kicad_pcb]
2022-05-15 Create MatrixControllerI2C example
    [FlipDot34NanoSMD.kicad_pcb, FlipDot34NanoSMD.kicad_sch]
2022-05-18 Send bitmaps over I2c
2022-09-17 Add second I2C interface header
    [FlipDot34NanoSMD2.kicad_pcb, FlipDot34NanoSMD2.kicad_sch]
2022-09-18 Version 3 of the matrix controller board
    [FlipDot34NanoSMD3.kicad_pcb, FlipDot34NanoSMD3.kicad_sch]
2022-09-25 Bad Apple demo
    [Esp32x4.kicad_pcb, Esp32x4.kicad_sch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]
